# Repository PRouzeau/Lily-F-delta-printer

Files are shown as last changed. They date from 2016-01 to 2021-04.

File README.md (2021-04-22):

**"Lily" delta printer** built with strong wooden box structure and equipped with activated carbon filters<br>
The version 'F' is built with RRP Fisher components. Usable area diam 170mm x 242mm or diam 186mm x 225 mm<br>
To see the simulation of printer, run the "Delta_simulator.scad" in OpenScad <br>
The parameters of this simulation are defined in "data_Lily_F.scad" <br>
effector simulation use stl files created in "Effector_Lily_F.scad" <br>
To creates STL file, define a part Number in "data_Lily_F.scad" in OpenScad <br>
To creates STL files for the effector, define a part Number in "Effector_Lily_F.scad" in OpenScad <br>
<br>
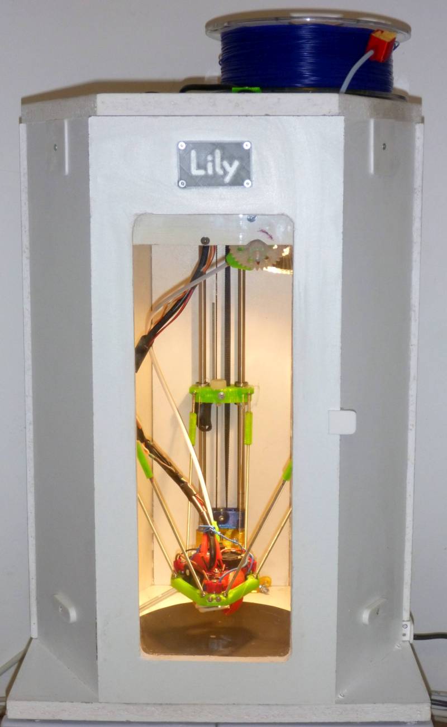
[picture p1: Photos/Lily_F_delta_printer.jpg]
Lily F photo, version D170xH242


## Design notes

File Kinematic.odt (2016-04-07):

As already published in this forum, I am using the wire tensioning system on my two printers since 6 month now, first on the D-Box http://rouzeau.net/Print3D/DBox, then on the Lily http://rouzeau.net/Print3D/Lily.

Retainers are magnets on the D-Box, and rubbers bands on the Lily, to save weight.

The bowden tube tend to pull the hotend support for probe points at the largest diameter, so I had to increase the hotend support pulling value to a minimum. I settled to ~1kg for both machines.

The repeatability is very good in a fixed context, however, the load needed to operate the ‘sensor’ make you machine to deflect of a significant amount, giving a probing offset. As the machine deformations are not the same on all the bed area, you shall individualise offset for each probe point, with calibration done with the sheet paper method.

The offset variability depends a lot of the overall machine stiffness. For the D-Box, I had initially an offset of ~0.4~-0.5mm, with a variability of ~0.15mm. When I replaced the arms by stiffer ones (the weak point was the screwing in plastic on the arms themselves), that reduced sufficiently the offset variability between all points that I abandoned individual offset to a common one, which is now a constant of 0.5 mm for all probing points.

The Lily, while a smaller machine, is a bit less robust (its mechanics cames from the Fisher Delta) and the offset variability remains significant throughout the bed, with values ranging from 0.35 to 0.45 (I have eliminated one point which is off plane).

The only problems I experienced so far :

*I had to retighten the standoffs as their screws tend to became loose with time.

*Heating the D-Box chamber (~70°C)/the bed (tested at 130°C) have driven to effector bending due to wire tension, needing to raise the effector to avoid magnet contacts making the sensor inoperative. The material used (PETG) cannot cope with these temperature tests.

In the Lily « F », there is only yet an halogen spot of 50W which raise slowly the chamber temperature to ~38°C while printing. I will install a heated bed of 100~120W, and will report the obtained temperature (expected below 55°C for Bed 100°C).

ABS may be a better material than PETG, but was not possible for me when I built both printers (no heat bed).

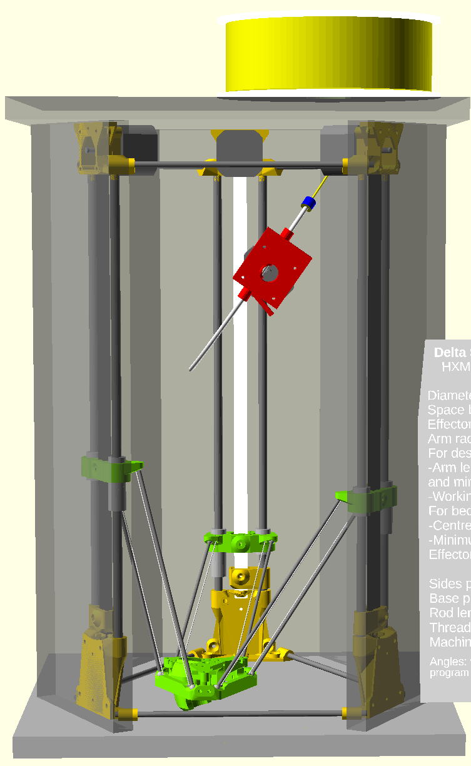
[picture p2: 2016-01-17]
Photos/Lily_F_simulation.png

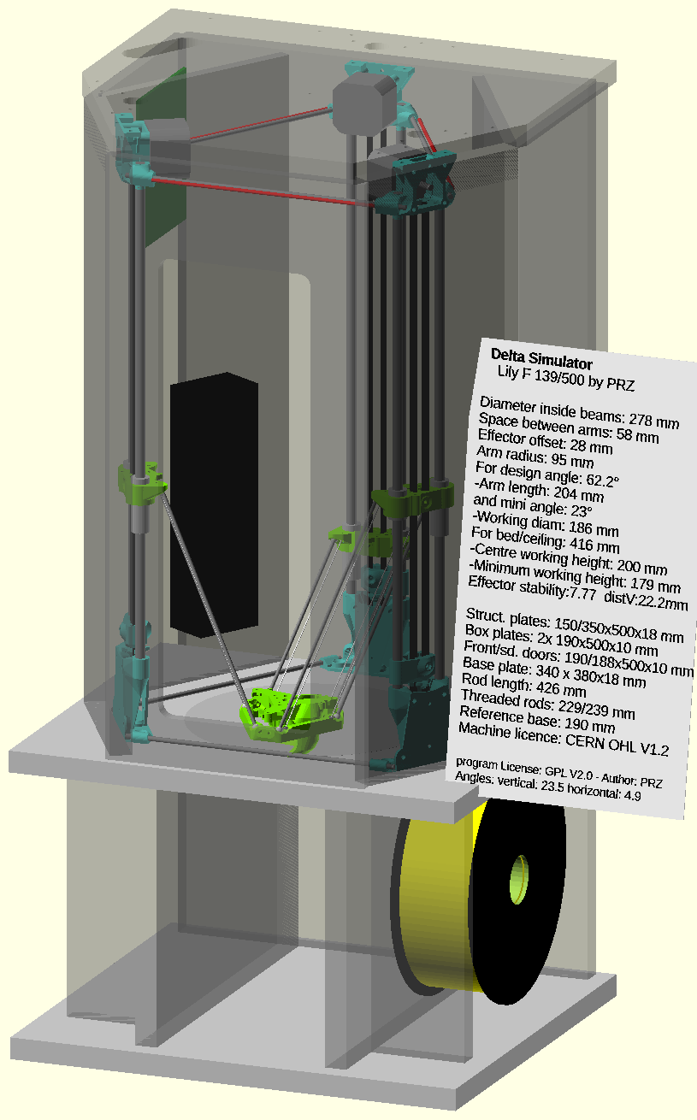
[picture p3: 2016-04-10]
Photos/Lily_F_with_support.png

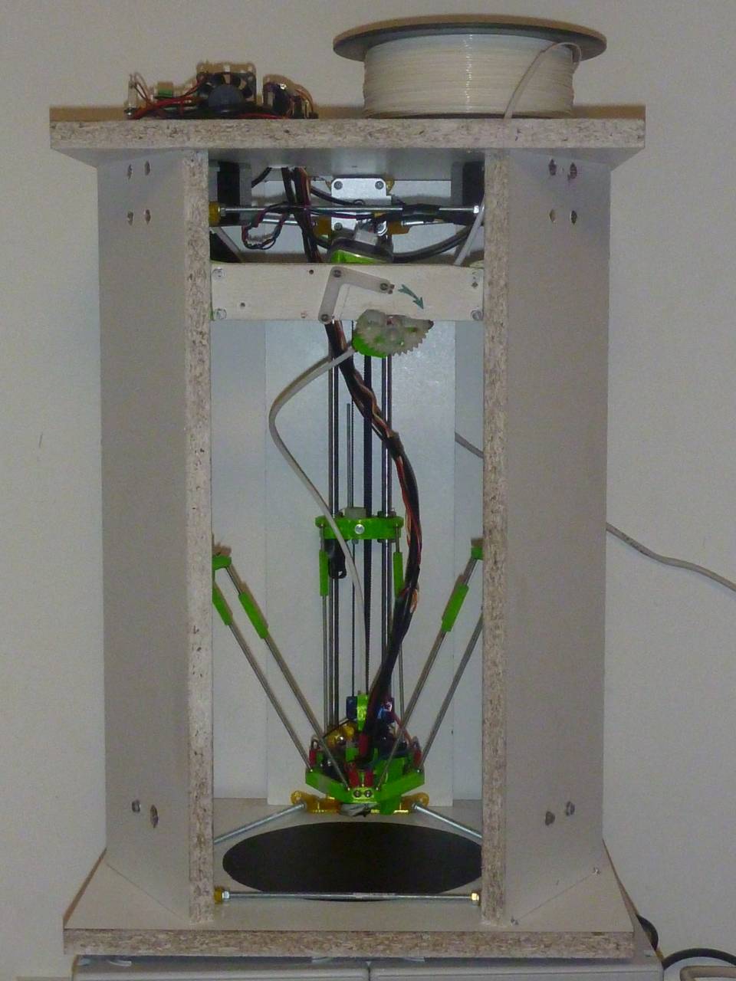
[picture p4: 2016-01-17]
Photos/Lily_F_not_enclosed.jpg

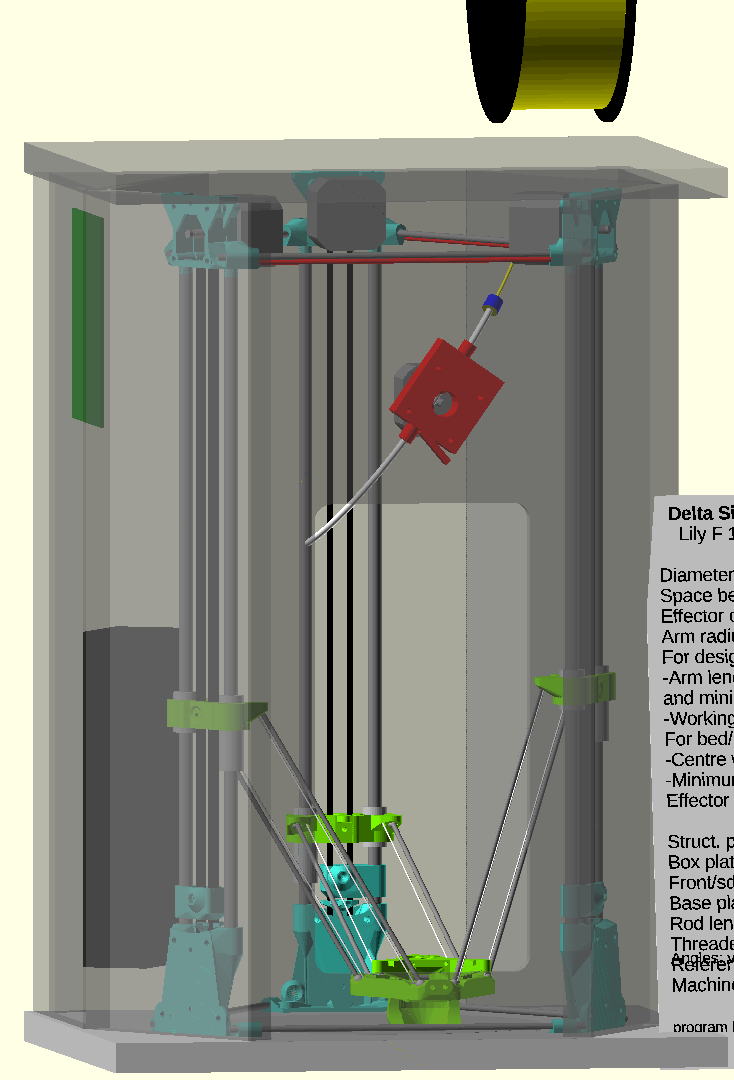
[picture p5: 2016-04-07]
Photos/Lily_F_simulation_boxed.png

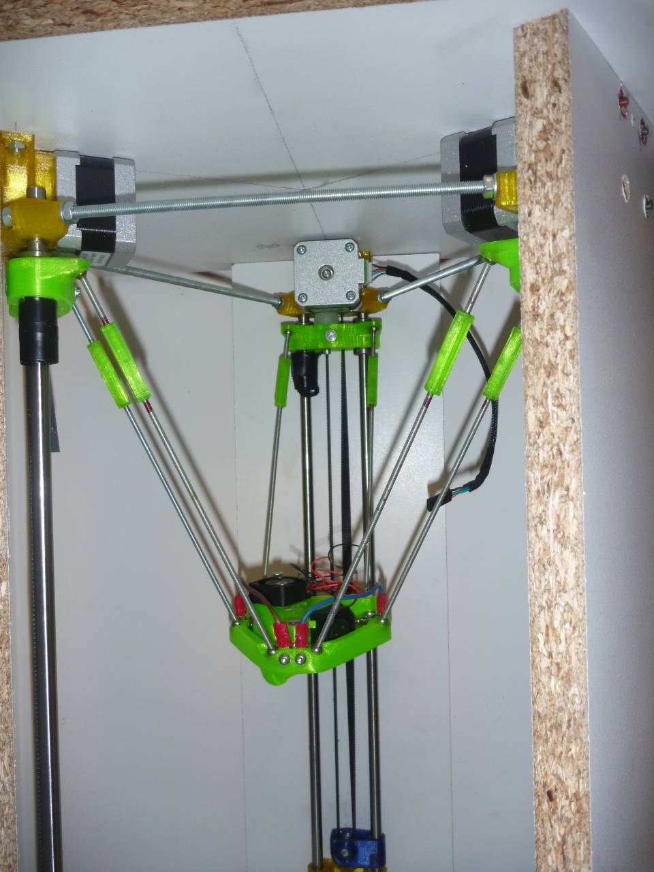
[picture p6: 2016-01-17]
Photos/Lily_F_motors.jpg

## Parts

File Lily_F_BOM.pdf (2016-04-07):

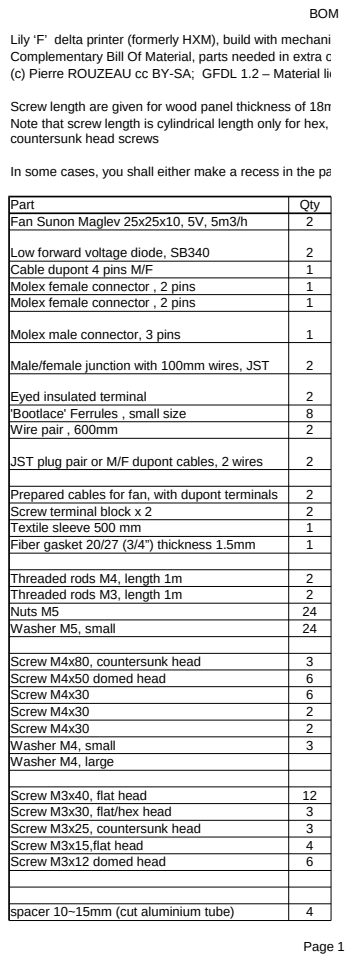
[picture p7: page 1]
BOM; Part; Qty; Fan Sunon Maglev 25x25x10, 5V, 5m3/h; Low forward voltage diode, SB340; Cable dupont 4 pins M/F; Molex female connector , 2 pins; Molex male connector, 3 pins; Male/female junction with 100mm wires, JST; Eyed insulated terminal; 'Bootlace' Ferrules , small size; Wire pair , 600mm; JST plug pair or M/F dupont cables, 2 wires; Prepared cables for fan, with dupont terminals; Screw terminal block x 2; Textile sleeve 500 mm; Fiber gasket 20/27 (3/4”) thickness 1.5mm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

Lily ‘F’ delta printer (formerly HXM), build with mechanical parts of the Fisher delta.
Complementary Bill Of Material, parts needed in extra of the Fisher parts
(c) Pierre ROUZEAU cc BY-SA; GFDL 1.2 – Material licence CERN OHL V1.2 – January 2016

Screw length are given for wood panel thickness of 18mm
Note that screw length is cylindrical length only for hex, flat, domed, .. head screws, but is total screw length for
countersunk head screws

In some cases, you shall either make a recess in the panel, or use cutted screws

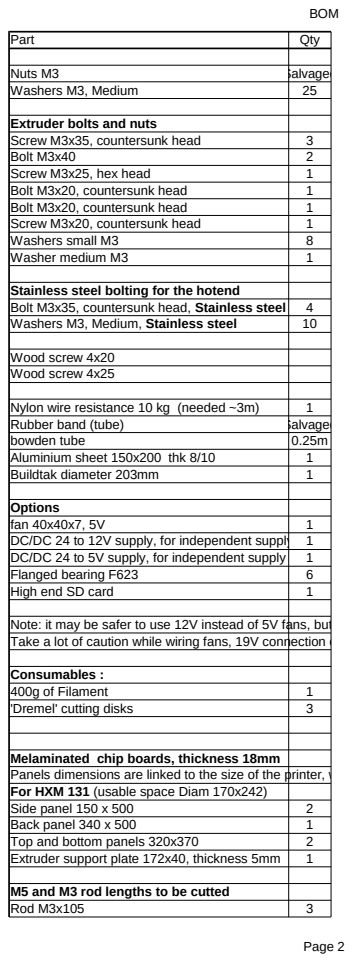
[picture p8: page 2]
Part; Qty; Nuts M3; Salvaged; Washers M3, Medium; Screw M3x35, countersunk head; Bolt M3x40; Screw M3x25, hex head; Bolt M3x20, countersunk head; Screw M3x20, countersunk head; Washers small M3; Washer medium M3; Wood screw 4x20 Wood screw 4x25; Nylon wire resistance 10 kg (needed ~3m); Rubber band (tube); bowden tube; Aluminium sheet 150x200 thk 8/10; Buildtak diameter 203mm; fan 40x40x7, 5V; DC/DC 24 to 5V supply, for independent supply; Flanged bearing F623; High end SD card; Consumables :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

Extruder bolts and nuts

Stainless steel bolting for the hotend
Bolt M3x35, countersunk head, Stainless steel
Washers M3, Medium, Stainless steel

Options
DC/DC 24 to 12V supply, for independent supply 1

Note: it may be safer to use 12V instead of 5V fans, but you need a DC/DC converter 19V→12V
Take a lot of caution while wiring fans, 19V connection on 5V input will burn the board

Melaminated chip boards, thickness 18mm
Panels dimensions are linked to the size of the printer, which is defined by the radius of the rod axis
For HXM 131 (usable space Diam 170x242)

M5 and M3 rod lengths to be cutted

Part | Qty
Measurement stick 172mm | 1
Rod M5x214 | 3
Rod M5x225 | 3
Rod M3x40 | 6
Rod M3x147 | 6

For HXM139/500
Measurement stick 188mm | 1
Rod M5x230 | 3
Rod M5x241 | 3
Rod M3x40 | 6
Rod M3x161 | 6

For HXM131/500 (usable space Diam 170x242)

Usage
hotend fan + part fan

Prolonge 1 motor wire
5V connection on board
Connect controlled fan on board – use only 1 wire

connect the fans on screw terminals Adjustable fan and effector sensor connection

Fan plugs on effector
Fan connection to 5V
Effector cables maintain
Hotend insulator

triangle, cuts 3x225, 3x214 arms 6x40, 6x147

triangle rods

Tensioner screw
bottom attach rod locks
bottom support attach to wall Top attach motor support
Top attach extruder
Tensioner screw

Motor attach
carriage lock
tensioner bearing shaft
extruder plate attach
kinematic cylinders

Board support

secure the fan power supply, other solution remove board LED

Connect fixed fan on existing loom – could be replaced by soldering
connect effector sensor and adjustable fan on hotend side
connect effector sensor standoff. Existing not usable because insufficient clearance

Connection of the calibration sensor and of the controlled fan on Effector

Usage

Salvaged

Motor attach
Tensioner
Main gear axis
Bearing axis
Lever axis
Motor attach

1rst washer on main gear

Hotend attach

arms tension
effector maintain
filament inlet
board cover
printing surface

board cooling
to use 12V fans instead of 5V – safer

belt pulleys
To speed up transfer – could go up to 350 kB/sec

The base material
To cut M3 rods. M5 rods are sawed

switch actuation (option)

Usage

Bottom triangle
Top triangle
Arm, short side
Arms, long side (for arms L190mm)

Bottom triangle
Top triangle
Arm, short side
Arms, long side (for arms L204mm)

Weights

Printed parts for Lily F delta Printer (c) Pierre ROUZEAU - cc BY-SA Weights in grams, time in minutes

Part | Weight | Comments
Tensioner | 7 | 60Layer 0.3
base support | 30 | 240Layer 0.3
motor support | 20 | 150Layer 0.3
carriage | 15 | 175Layer 0.3
rod joint | 2 | 20Layer 0.3
74 222
hotend support | 20 | 85Layer 0.25
effector | 19 | 48Layer 0.3
39
arm links (6) | - | 8 | Layer 0.3
extruder base | 16 | 50Layer 0.25
extruder lever | 7 | - | Layer 0.2
pinion | 4 | - | Layer 0.2
gear | 8 | 90Layer 0.2 | gears+lever common print
35
Extruder plate brackets | 7 | 7 | 20Layer 0.3
Spool support | - | - | Layer 0.3
Axis | - | Layer 0.3
Spool ring | - | 30- | Layer 0.3
90 | all spool

341
15.30

Direct extruder print is only 50 min, so that same 1h and an half on printing time.

The hotend support shall absolutely be in plastic somewhat resistant to heat. PLA WILL melt.

The given times are for a hotend with long heat zone adapted for PETG printing.
Also, there is controlled cooling, which allow shorter cooling time and faster prints for some parts For the fisher, printing time may be increased approximately by 20%

Time
(total)

If printed on the Fisher in PETG, there is no point to print in layer 0.3, as the extruder cannot have sufficient flowrate at 80 mm/s, so you could print with layer 0.3 and reduced speed (~50mm/s) or with layers 0.25 at full speed (80 mm/s). Temperature shall be high, but you may face problems for parts with bridging or small area.

Weights Standard

Printed parts for Lily ‘F’ (formerly HXM) delta Printer (c) Pierre ROUZEAU - cc BY-SA Weights in grams, time in minutes

Part | Nb | Weight | Comments
Tensioner | 6 or 7 | 7 | | 60Layer 0.3
foot | 2 | 12 | - | Layer 0.3
Intermediate support | 3 | 7 | | 145Layer 0.3
motor support | 4 | 20 | | 150Layer 0.3
carriage | 5 | 15 | | 175Layer 0.3
tensioner thumbwheel | 8 | 1 | | 5Layer 0.3
arm links (6) | 9 | 2 | | 20Layer 0.3
| | 64 192
hotend support 1 | | 9 | - | Layer 0.3
hotend support 2 | | 6 | | 38Layer 0.3
effector | | 19 | | 48Layer 0.3
Duct | 4 | 15
28
Direct extruder base | | 10 | - | Layer 0.3
Tensioner | | 1 | - | Layer 0.3
extruder lever | | 6 | - | Layer 0.25
thumbwheel | | 1 | | Layer 0.25
55
18
Extruder plate brackets | 7 | 7 | 20Layer 0.3
Board supports | 11 | 4 | | 14Layer 0.3
Glass supports | 8 | 24
12
Spool support | | - | - | Layer 0.3
Axis | | - | | Layer 0.3
Spool ring | | - | 30 - | Layer 0.3
90 | all spool

287
| | | 14.32

The hotend support shall absolutely be in plastic somewhat resistant to heat. PLA WILL melt.

The given times are for a hotend with long heat zone adapted for PETG printing.
Also, there is controlled cooling, which allow shorter cooling time and faster prints for some parts

Time
(total)
Part 6 for plain bearings, part 7 for flanged bearings

If printed on the Fisher in PETG, there is no point to print in layer 0.3, as the extruder cannot have sufficient flowrate at 80 mm/s, so you could print with layer 0.3 and reduced speed (~50mm/s) or with layers 0.25 at full speed (80 mm/s). Temperature shall be high, but you may face problems for parts with bridging or small area.

Weights Standard

For the fisher, printing time may be increased approximately by 20%

Weights Standard

“c:\Program Files\OpenSCAD\
“c:\Program Files\OpenSCAD\openscad” data_HXM.scad

'c:\Program Files\OpenSCAD\openscad.exe' -o Lily_part3 -D part=3 data_HXM.scad

Weights Standard

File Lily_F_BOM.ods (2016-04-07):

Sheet: BOM
Lily ‘F’ delta printer (formerly HXM), build with mechanical parts of the Fisher delta.
Complementary Bill Of Material, parts needed in extra of the Fisher parts
(c) Pierre ROUZEAU cc BY-SA; GFDL 1.2 – Material licence CERN OHL V1.2 – January 2016
Screw length are given for wood panel thickness of 18mm
Note that screw length is cylindrical length only for hex, flat, domed, .. head screws, but is total screw length for countersunk head screws
In some cases, you shall either make a recess in the panel, or use cutted screws
Part | Qty | Usage
Fan Sunon Maglev 25x25x10, 5V, 5m3/h | 2 | hotend fan + part fan
Low forward voltage diode, SB340 | 2 | secure the fan power supply, other solution remove board LED
Cable dupont 4 pins M/F | 1 | Prolonge 1 motor wire
Molex female connector , 2 pins | 1 | 5V connection on board
Molex female connector , 2 pins | 1 | Connect controlled fan on board – use only 1 wire
Molex male connector, 3 pins | 1 | Connect fixed fan on existing loom – could be replaced by soldering
Male/female junction with 100mm wires, JST | 2 | connect effector sensor and adjustable fan on hotend side
Eyed insulated terminal | 2 | connect effector sensor standoff. Existing not usable because insufficient clearance
'Bootlace' Ferrules , small size | 8 | connect the fans on screw terminals
Wire pair , 600mm | 2 | Adjustable fan and effector sensor connection
JST plug pair or M/F dupont cables, 2 wires | 2 | Connection of the calibration sensor and of the controlled fan on Effector
Prepared cables for fan, with dupont terminals | 2 | Fan plugs on effector
Screw terminal block x 2 | 2 | Fan connection to 5V
Textile sleeve 500 mm | 1 | Effector cables maintain
Fiber gasket 20/27 (3/4”) thickness 1.5mm | 1 | Hotend insulator
Threaded rods M4, length 1m | 2 | triangle, cuts 3x225, 3x214
Threaded rods M3, length 1m | 2 | arms 6x40, 6x147
Nuts M5 | 24
Washer M5, small | 24 | triangle rods
Screw M4x80, countersunk head | 3 | Tensioner screw
Screw M4x50 domed head | 6 | bottom attach rod locks
Screw M4x30 | 6 | bottom support attach to wall
Screw M4x30 | 2 | Top attach motor support
Screw M4x30 | 2 | Top attach extruder
Washer M4, small | 3 | Tensioner screw
Washer M4, large
Screw M3x40, flat head | 12 | Motor attach
Screw M3x30, flat/hex head | 3 | carriage lock
Screw M3x25, countersunk head | 3 | tensioner bearing shaft
Screw M3x15,flat head | 4 | extruder plate attach
Screw M3x12 domed head | 6 | kinematic cylinders
spacer 10~15mm (cut aluminium tube) | 4 | Board support
Nuts M3 | Salvaged
Washers M3, Medium | 25
Extruder bolts and nuts
Screw M3x35, countersunk head | 3 | Motor attach
Bolt M3x40 | 2 | Tensioner
Screw M3x25, hex head | 1 | Main gear axis
Bolt M3x20, countersunk head | 1 | Bearing axis
Bolt M3x20, countersunk head | 1 | Lever axis
Screw M3x20, countersunk head | 1 | Motor attach
Washers small M3 | 8
Washer medium M3 | 1 | 1rst washer on main gear
Stainless steel bolting for the hotend
Bolt M3x35, countersunk head, Stainless steel | 4 | Hotend attach
Washers M3, Medium, Stainless steel | 10
Wood screw 4x20
Wood screw 4x25
Nylon wire resistance 10 kg (needed ~3m) | 1 | arms tension
Rubber band (tube) | Salvaged | effector maintain
bowden tube | 0.25m | filament inlet
Aluminium sheet 150x200 thk 8/10 | 1 | board cover
Buildtak diameter 203mm | 1 | printing surface
Options
fan 40x40x7, 5V | 1 | board cooling
DC/DC 24 to 12V supply, for independent supply | 1 | to use 12V fans instead of 5V – safer
DC/DC 24 to 5V supply, for independent supply | 1
Flanged bearing F623 | 6 | belt pulleys
High end SD card | 1 | To speed up transfer – could go up to 350 kB/sec
Note: it may be safer to use 12V instead of 5V fans, but you need a DC/DC converter 19V→12V
Take a lot of caution while wiring fans, 19V connection on 5V input will burn the board
Consumables :
400g of Filament | 1 | The base material
'Dremel' cutting disks | 3 | To cut M3 rods. M5 rods are sawed
Melaminated chip boards, thickness 18mm
Panels dimensions are linked to the size of the printer, which is defined by the radius of the rod axis
For HXM 131 (usable space Diam 170x242)
Side panel 150 x 500 | 2
Back panel 340 x 500 | 1
Top and bottom panels 320x370 | 2
Extruder support plate 172x40, thickness 5mm | 1
M5 and M3 rod lengths to be cutted
Rod M3x105 | 3 | switch actuation (option)
For HXM131/500 (usable space Diam 170x242)
Measurement stick 172mm | 1
Rod M5x214 | 3 | Bottom triangle
Rod M5x225 | 3 | Top triangle
Rod M3x40 | 6 | Arm, short side
Rod M3x147 | 6 | Arms, long side (for arms L190mm)
For HXM139/500
Measurement stick 188mm | 1
Rod M5x230 | 3 | Bottom triangle
Rod M5x241 | 3 | Top triangle
Rod M3x40 | 6 | Arm, short side
Rod M3x161 | 6 | Arms, long side (for arms L204mm)

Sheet: Weights
Printed parts for Lily F delta Printer (c) Pierre ROUZEAU - cc BY-SA
Weights in grams, time in minutes
Part | Weight |  | Time (total) |  | Comments
Tensioner | 7 |  | 60 | Layer 0.3
base support | 30 |  | 240 | Layer 0.3
motor support | 20 |  | 150 | Layer 0.3
carriage | 15 |  | 175 | Layer 0.3
rod joint | 2 |  | 20 | Layer 0.3
 | 74 | 222
hotend support | 20 |  | 85 | Layer 0.25
effector | 19 |  | 48 | Layer 0.3
 |  | 39
arm links (6) | - | 8 |  | Layer 0.3
extruder base | 16 |  | 50 | Layer 0.25
extruder lever | 7 |  | - | Layer 0.2
pinion | 4 |  | - | Layer 0.2
gear | 8 |  | 90 | Layer 0.2 | gears+lever common print
 |  | 35
Extruder plate brackets | 7 | 7 | 20 | Layer 0.3
Spool support | - |  | - | Layer 0.3
Axis | - |  |  | Layer 0.3
Spool ring | - | 30 | - | Layer 0.3
 |  |  | 90 |  | all spool
 |  | 341
 |  |  | 15.30
Direct extruder print is only 50 min, so that same 1h and an half on printing time.
If printed on the Fisher in PETG, there is no point to print in layer 0.3, as the extruder cannot have sufficient flowrate at 80 mm/s, so you could print with layer 0.3 and reduced speed (~50mm/s) or with layers 0.25 at full speed (80 mm/s). Temperature shall be high, but you may face problems for parts with bridging or small area.
The hotend support shall absolutely be in plastic somewhat resistant to heat. PLA WILL melt.
The given times are for a hotend with long heat zone adapted for PETG printing.
Also, there is controlled cooling, which allow shorter cooling time and faster prints for some parts
For the fisher, printing time may be increased approximately by 20%

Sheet: Weights Standard
Printed parts for Lily ‘F’ (formerly HXM) delta Printer (c) Pierre ROUZEAU - cc BY-SA
Weights in grams, time in minutes
Part | Nb | Weight |  | Time (total) |  | Comments
Tensioner | 6 or 7 | 7 |  | 60 | Layer 0.3 | Part 6 for plain bearings, part 7 for flanged bearings | “c:\Program Files\OpenSCAD\openscad” -o Lily_part11.stl -Dpart=11 data_HXM.scad | 'c:\Program Files\OpenSCAD\openscad.exe' -o Lily_part3 -D part=3 data_HXM.scad
foot | 2 | 12 |  | - | Layer 0.3 |  | “c:\Program Files\OpenSCAD\openscad” data_HXM.scad
Intermediate support | 3 | 7 |  | 145 | Layer 0.3
motor support | 4 | 20 |  | 150 | Layer 0.3
carriage | 5 | 15 |  | 175 | Layer 0.3
tensioner thumbwheel | 8 | 1 |  | 5 | Layer 0.3
arm links (6) | 9 | 2 |  | 20 | Layer 0.3
 |  | 64 | 192
hotend support 1 |  | 9 |  | - | Layer 0.3
hotend support 2 |  | 6 |  | 38 | Layer 0.3
effector |  | 19 |  | 48 | Layer 0.3
Duct |  | 4 |  | 15
 |  |  | 28
Direct extruder base |  | 10 |  | - | Layer 0.3
Tensioner |  | 1 |  | - | Layer 0.3
extruder lever |  | 6 |  | - | Layer 0.25
thumbwheel |  | 1 |  |  | Layer 0.25
 |  |  |  | 55
 |  |  | 18
Extruder plate brackets |  | 7 | 7 | 20 | Layer 0.3
Board supports | 11 | 4 |  | 14 | Layer 0.3
Glass supports |  | 8 |  | 24
 |  |  | 12
Spool support |  | - |  | - | Layer 0.3
Axis |  | - |  |  | Layer 0.3
Spool ring |  | - | 30 | - | Layer 0.3
 |  |  |  | 90 |  | all spool
 |  |  | 287
 |  |  |  | 14.32
If printed on the Fisher in PETG, there is no point to print in layer 0.3, as the extruder cannot have sufficient flowrate at 80 mm/s, so you could print with layer 0.3 and reduced speed (~50mm/s) or with layers 0.25 at full speed (80 mm/s). Temperature shall be high, but you may face problems for parts with bridging or small area.
The hotend support shall absolutely be in plastic somewhat resistant to heat. PLA WILL melt.
The given times are for a hotend with long heat zone adapted for PETG printing.
Also, there is controlled cooling, which allow shorter cooling time and faster prints for some parts
For the fisher, printing time may be increased approximately by 20%

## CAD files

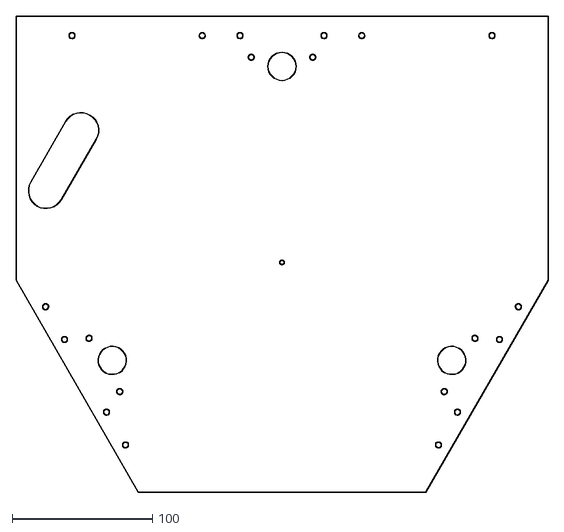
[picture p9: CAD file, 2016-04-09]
DXF/Lily_F_139_500_65_top_panel.dxf
380.0 x 340.0

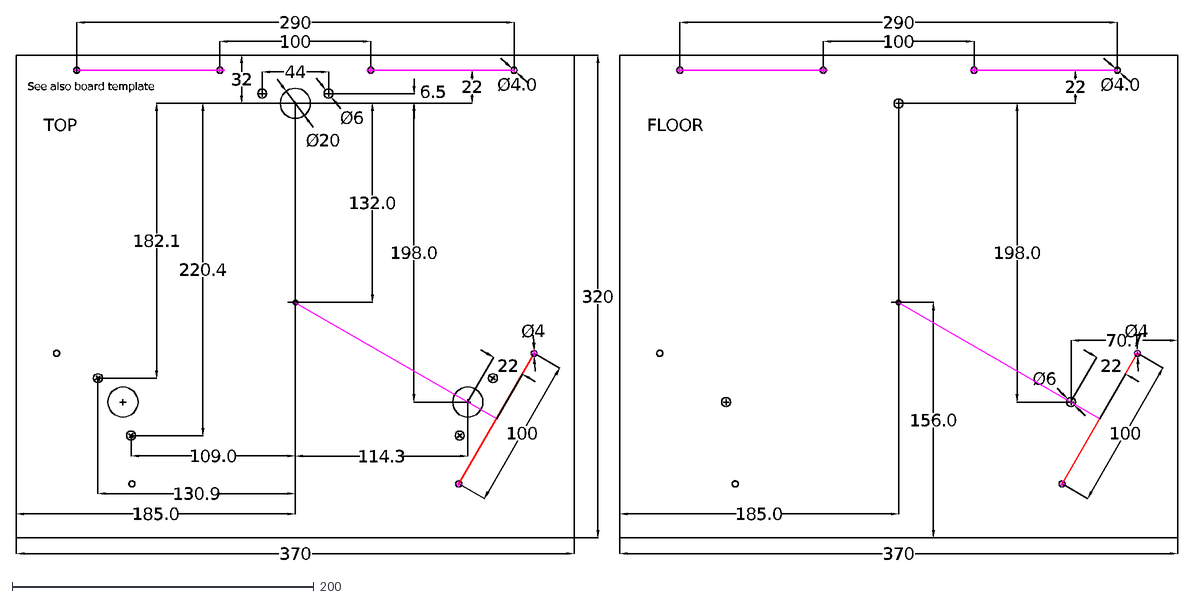
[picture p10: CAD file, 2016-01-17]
Lily_F_131_500_top_bottom_template.dxf
198.0
114.3
32
185.0
6.5
44
130.9
109.0
220.4
182.1
132.0
TOP
Ø20
Ø6
70.7
320
156.0
FLOOR
See also board template
Ø4.0
100
22
290
Ø4
370

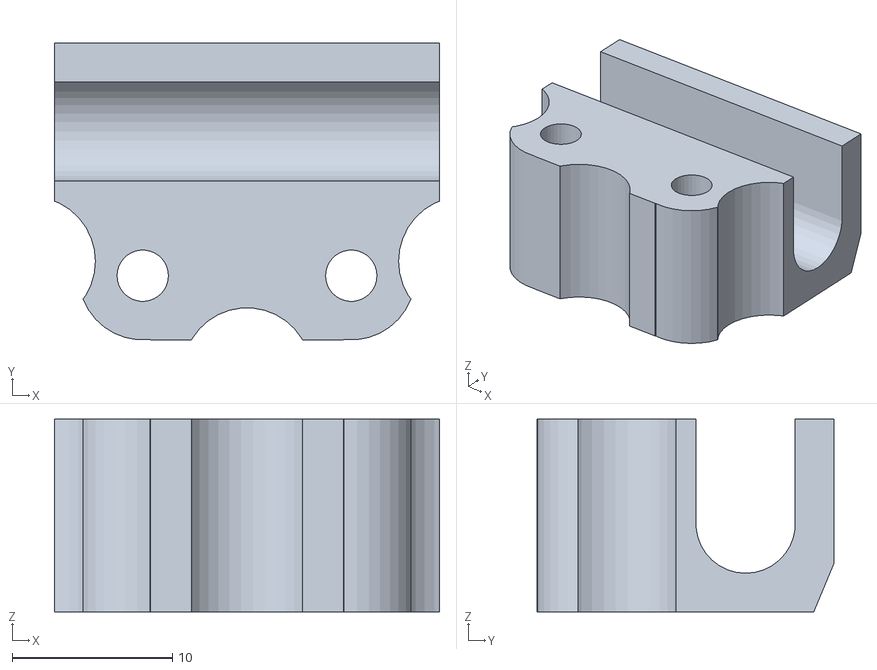
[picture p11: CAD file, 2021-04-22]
STL/Lily_32_cable_retainer.stl
24.0 x 18.5 x 12.0

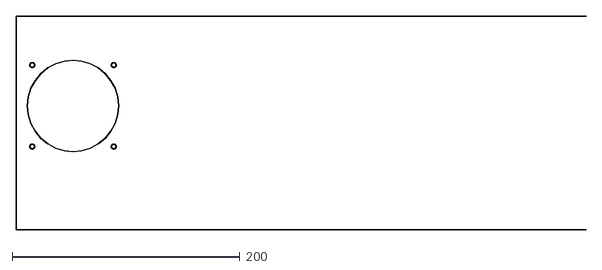
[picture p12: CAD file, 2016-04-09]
DXF/Lily_F_139_500_55_left_door.dxf
500.0 x 187.5

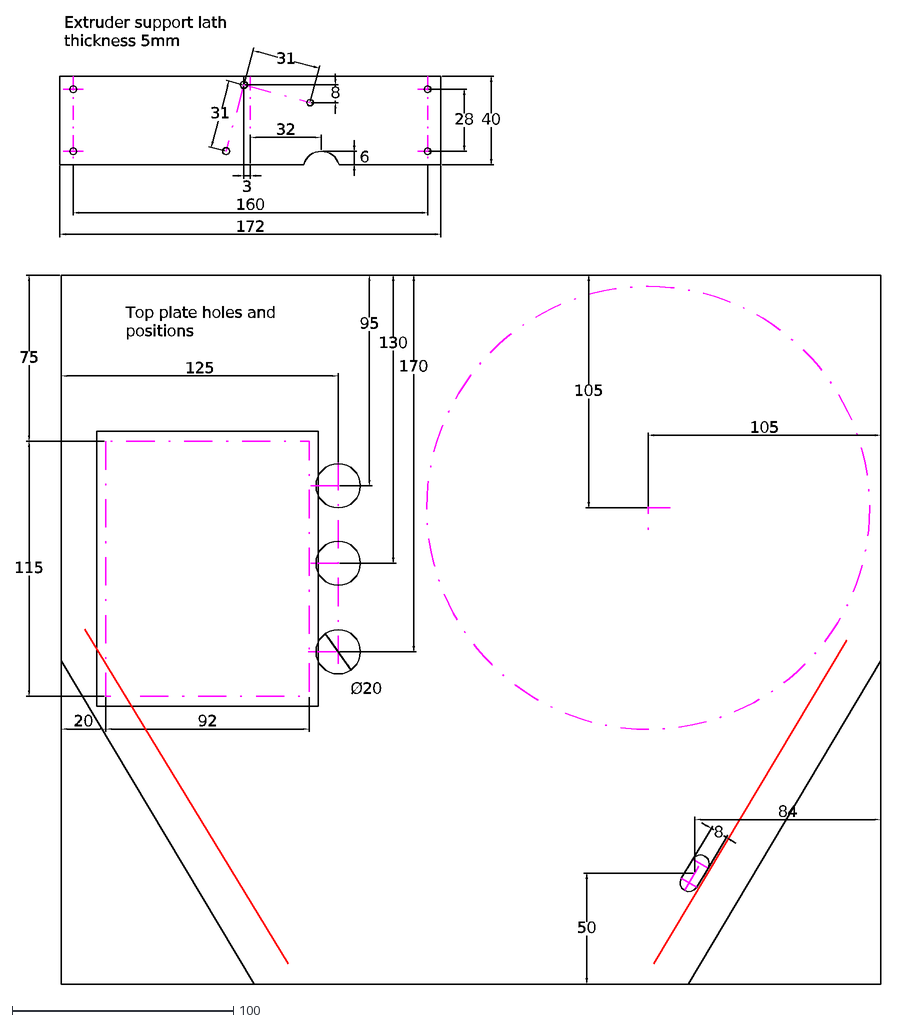
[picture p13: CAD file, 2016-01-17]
Lily_F_131_500_board_pos.dxf
20
92
75
115
125
130
170
105
84
50
95
8
31
3
172
160
40
28
32
6
Extruder support lath thickness 5mm
Ø20
Top plate holes and positions

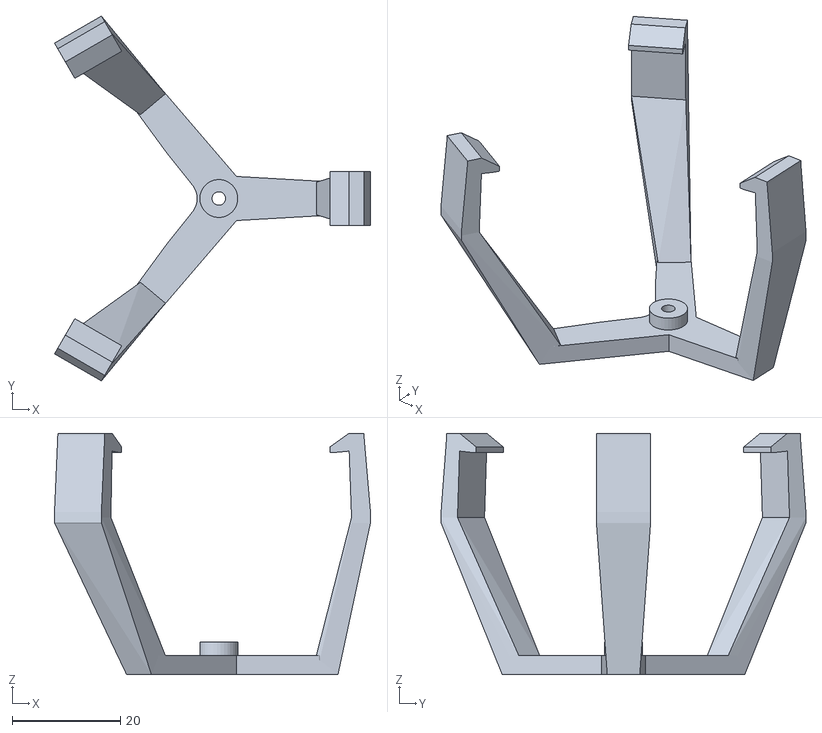
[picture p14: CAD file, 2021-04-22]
STL/Lily_33_effector_retainer.stl
58.3 x 67.4 x 44.5

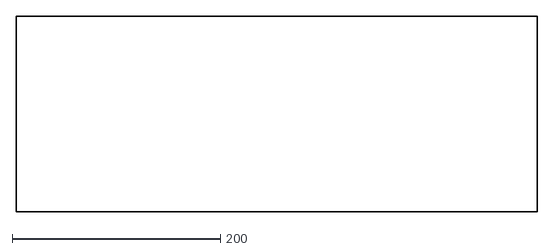
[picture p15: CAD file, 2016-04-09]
DXF/Lily_F_139_500_56_right_door.dxf
500.0 x 187.5

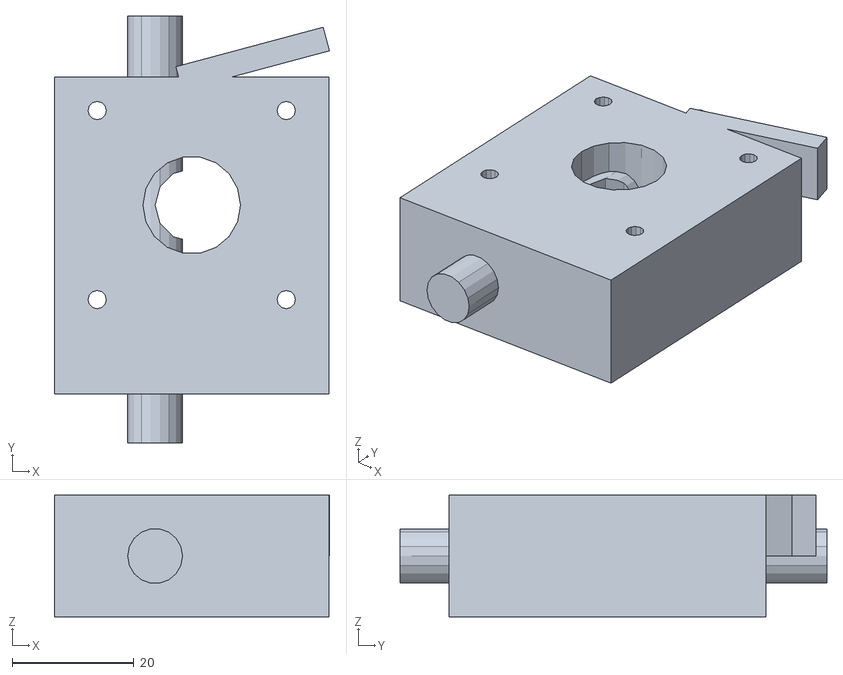
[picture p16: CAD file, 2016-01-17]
extruder.stl
45.1 x 70.0 x 20.0

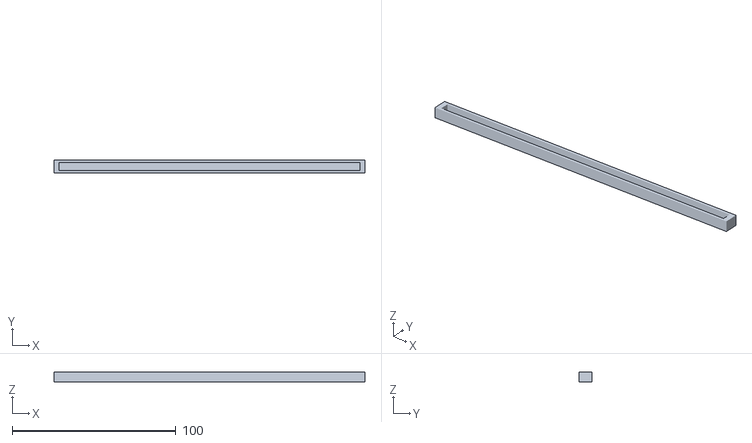
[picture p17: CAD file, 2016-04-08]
STL/Lily_F_139_reference_stick.stl
189.9 x 8.00 x 6.00

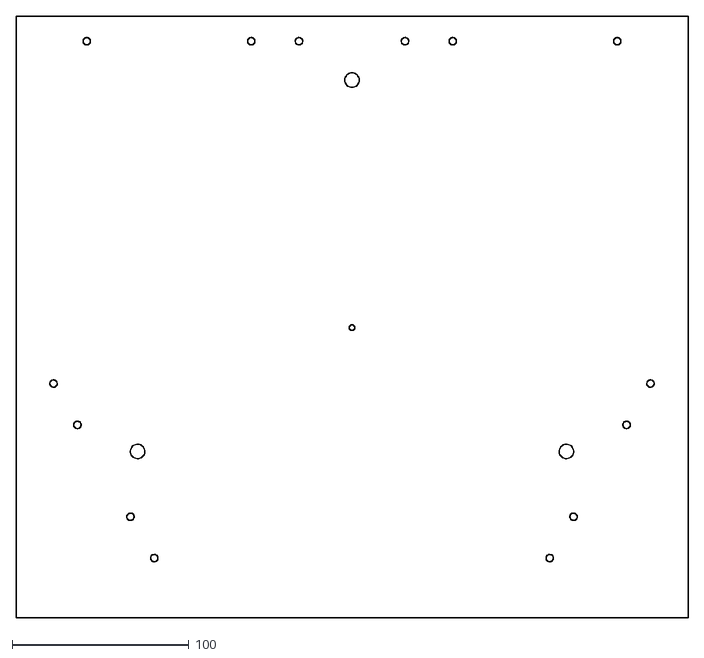
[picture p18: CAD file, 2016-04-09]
DXF/Lily_F_139_500_61_bottom.dxf
380.0 x 340.0

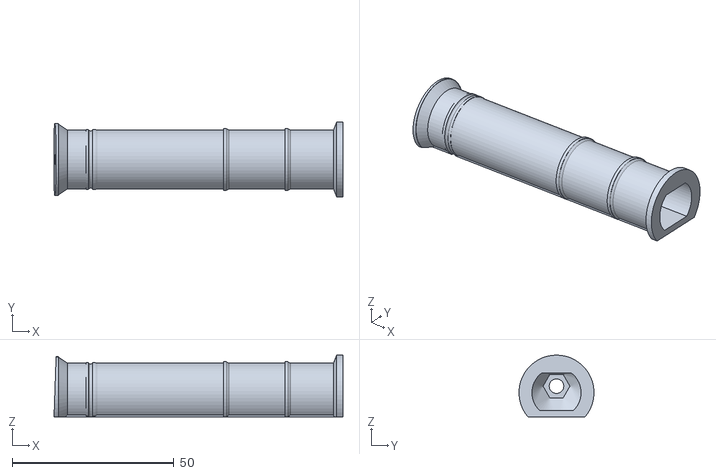
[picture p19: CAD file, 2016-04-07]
STL/Spigot90.stl
89.3 x 23.2 x 19.1

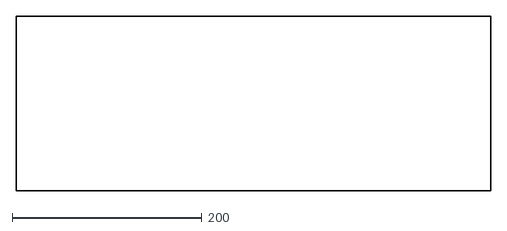
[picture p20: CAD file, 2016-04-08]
DXF/Lily_F_139_500_53_left_side.dxf
500.0 x 184.2

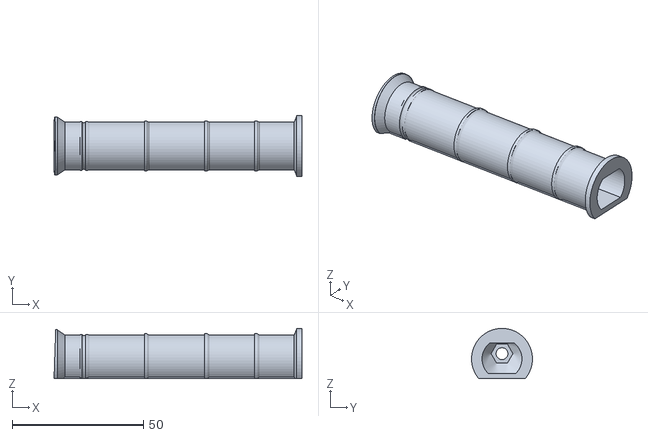
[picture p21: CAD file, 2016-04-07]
STL/Spigot95.stl
94.3 x 23.2 x 19.1

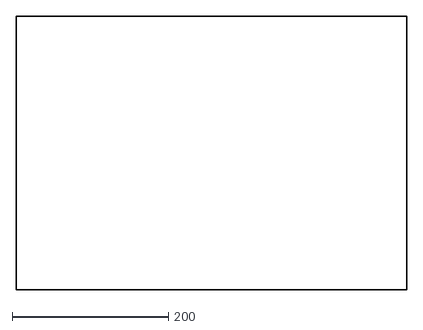
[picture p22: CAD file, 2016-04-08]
DXF/Lily_F_139_500_52_back_panel.dxf
500.0 x 350.0

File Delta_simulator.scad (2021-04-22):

// Parallel columns delta robot simulator, extracted from my Delta printer design.
// This simulator could emulate any delta travels, provided the parameters are accurate.
// Needs OpenScad 2015.03 or, for animations, the nightly versions.

// Play with it! you won't broke anything. See line 92 for existing datasets. 

// To run the animation click [View][Animate],a panel open in the bottom right of your screen. Set 10~25 in the FPS fied and 360 in the field 'Steps'. A lower number will make larger steps. You can manipulate the view during animation. 
// OpenScad official version 2015.03 have a lot of flickering during animation. This is corrected in the nightly versions, which I recommended to use.  
// Licence GPL V2.0 - Pierre ROUZEAU aka PRZ - 
// version 0.4.3 - 12 June 2015
// 25 May 2015 - add twin rods in addition of extrusion - display bot name - modifs for micros deltas (Fisher delta and Micro Delta) - allow user part build for effector, corners and carriage.
// 29 may 2015 - added internal comments to explain use. Frame order build modified for tranparent panels
// June - allow more personnalisation - review fan , spool - allow dataset text lines
// 12 June 15: 'square Delta' - 29 sept 15 'Zatsit' folded mechanic

//??? modifs -> Inversion rotation/translation on spool
//-- Data not redefined in dataset -------
$bArm= false;
$xtxt = 0; //???
$bdist = 0; // ? undef ?
$isAngle = false; // This is for Lily Big with steel angle rails
$extrusionwd = 0;

/*[Display]*/
//Build all the frame
$bAllFrame=true;
//Show details
$details=false;
//Remove box top
$noTop = false;
//Remove top column supports
$noTopSup = false;
//Complete Box (else only structural panels)
$boxed = true;
//Show side panels *in addition* to frame
$bSide = true; 
//??
$noCover=false;



/*[Movement]*/ 
//If no animation, the position is imposed by coordinates
panimation=false;
//hotend x coordinate - stay inside 
xe=50; 
//hotend y coordinate
ye=50;
//hotend z coordinate 
ze=0; 

/*/dimensions are in mm.
Delta_name = "Simulator example";
//-- Frame data -------------------------
beam_int_radius = 175; // radius inside the rectangular columns - used as reference radius
 // if columns are replaced with rods this is the radius of the rod axis plane. 
hbase = 60; // height of the base structure
htotal = 680; // total height, including base and top structure
bed_level = 8; // distance between the top of the bottom structure and the top of the bed.
extrusion = 20;
rod_space = 0; //if > 0 set two rods instead of one extrusion, diameter based on extrusion
  // if set, reference radius is rod axis plane and not extrusion face  
railthk   = 0;  // rail thickness. if > 0, show a cuboid simulating a sliding rail
railwidth = 0; 
rail_base = 0; // base of the rail, which could be higher than bed plate

//-- Carriage data --------------------
car_hor_offset=20; //Carriage: horizontal distance between the articulation and the internal of the columns
car_vert_dist=27;  //Carriage: vertical articulation distance/reference plane (at the top of the carriage) 
hcar=75; // carriage height - no effect on travel
dia_ball = 10; 
dia_arm  = 68;

//-- Effector data ----------------------
eff_hor_offset=28; //Distance effector center/articulations Kossel mini: 20, Rostock max: 33mm
eff_vert_dist = 12; //Vertical distance between the bottom of effector and the articulations axis

//-- General design data ----------------
arm_space=50; // space between the arms
wire_space = 0 ; // space between tensioning wire
top_clearance=10; // clearance between top of the carriage and top structure
delta_angle = 62; //key travel design: arm angle/horizontal for centered effector.
//Will only define the arm length and travels. Does not modify parts. 57~63°
//62° gives slightly longer arms and a near maximum practical usable space with vertical arms while nearing columns (if the iminimum angle is 20°). For a 3D printer, great care shall be done while installing fans which could easily conflict with columns. fan shall be installed 60° from the column and protrude on flat side.
//Reachable area is a rounded triangular shape, with the ends pointed on columns, hence the real limitation of travel is dictated by the clearance on columns. You have the option to define a rough belt simulation, which will show the conflicts - see below.
//  A clever positioning allows elongated parts to be slightly longer than the theoretical usable diameter

arm_length = 0; // Alternatively, you could define the arm length, which will supersedes the design angle - If too long, you will have problem with the animation (reachable area too large drive to overpass vertical for the arms). Set to 0 give priority to the angle. arm length is given axis to axis. 
 
mini_angle = 20; //minimum angle/horizontal. 20° is generally considered as the practical limit. That will not modify the design, only give you an approximate information  about the maximum possible range. The range is not really circular, but will be considered so for practical reasons. You could go below 20°, but there is no real point, because when the other arms are nearing vertical, the effector bang the columns. Also, it drives to dynamic problems (a small effector move need a large carriage move), extra loads and effector loss of stability.

hotend_vert_dist = 20;//vertical distance between hotend nozzle and effector bottom plate. depends from the effector design and hotend type.

//Frame details
frame_corner_radius=1.5*extrusion; //modify corner shape radius.
frame_face_radius=280; // radius of the face. Shall be >> overall radius. 0 is flat
corner_offset = -3; //offset center of the corner sector / beam internal radius
housing_base = 0; // if = 0 no housing shown - usually set to hbase
housing_opening = 300;
belt_dist=0; //distance between the belt and the internal of the column. (belt face at the contact point with effector). if this data is different from 0, rough belt approximation will be shown, for conflict evaluation.


spool_diam = 200; // if spool_diameter > 0, spool shown on top - vertical axis
spool_thk  = 70;

//-- Miscellaneous stuff - no influence on movement ---
struct_color = "red";
moving_color = "deepskyblue";
bed_color = [0.5,0.5,0.5,0.5]; // transparent 

//Geometry
move_rot  = 0;
frame_rot = 30;

//--- Text display -----------------------
txtangle= -60;
txtzpos = 320;

//*/

/*[Hidden]*/
// geometry
rotAng2 = 120; // added angles definition for 'square' delta - see specific dataset
rotAng3 = 240;
railrot = -30;

//Indicate that the program just started (to impose camera position)
camPos = $vpr==[55,0,25];

/*
$vpd=camPos?2100:$vpd;      // camera distance: work only if set outside a module
$vpr=camPos?[80,0,42]:$vpr; // camera rotation
$vpt=camPos?[215,-90,420]:$vpt; //camera translation  */

//== data set included below will supersedes above data 
include <data_Lily_F.scad>  //- Data set for Hexagon minimum by PRZ
//=======================================
//$details=true;
//qpart = 1;

//--- Text display -----------------------
txtsize = beam_int_radius/16;
txtxpos = 0.8*beam_int_radius;
txtypos = 1.22*beam_int_radius;

//------------------------------------------
$fn=32; // smooth the cylinders

//$t=0.8377;

//-- imposing effector position (if defined, this will supersedes the animation equation)
// note that structure is rotated 30°, so x and y are rotated accordingly.

//Alternatively, you could impose the position in polar coordinates
/*
e_radius=90;
e_angle=-89;
ze=213; 
xe=e_radius*cos(e_angle);
ye=e_radius*sin(e_angle);   //*/

// if you ask for an unreachable point, arms and effector will not be displayed, without warning.

// Displayed angles are those of the arms attached to the back column
// Note that for long arms, the side angles you can see may not be acceptable for rod ends type 'traxxas', 'Igus' or equivalent and are a very limiting factor for the reachable area.

//echo_camera();

//=======================================
view(); //The animation will run around a cylinder based on the maximum reachable radius at the middle of the columns. If arms are sufficiently long, it will bang on columns, belts, etc.
*view_circle (working_dia,0); // view_circle (dia, height) - if off-limits - display may fail
// view_helix (); 

//--- dimensions calculations -----------
radius_cent = beam_int_radius-eff_hor_offset-car_hor_offset;
ar_length = (arm_length)?arm_length: radius_cent/cos(delta_angle); // center to center
d_angle = acos(radius_cent/ar_length);
ht_cent = radius_cent*tan(d_angle);
working_dia =2*(ar_length*cos(mini_angle)-beam_int_radius+car_hor_offset+eff_hor_offset);  
// calculate the maximum usable height - at center - at sides
// reference plane is the base of the effector
effVtPos = hbase+bed_level+hotend_vert_dist; // height of effector base plane; 
// add the base height
carVtPos =effVtPos +(ht_cent+car_vert_dist+eff_vert_dist); //top of carriage vertical position while the head is at bed level
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

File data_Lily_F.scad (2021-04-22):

include <Z_library.scad>  
include <X_utils.scad>
// Data Set for Delta printer -LilY - Jan-april 2015
// To be build from scratch (Lily 'S'), or with  standard Fisher components (Lily 'F')
// Copyright Pierre ROUZEAU AKA 'PRZ'
// Program license GPL 2.0
// documentation licence cc BY-SA and GFDL 1.2
// Design licence CERN OHL V1.2

part=0; //[0:None -Library-, 1:Elevated foot (Fisher rods), 2:Flat foot (rods down to floor), 3:Wall support (for non elevated foot), 4:Motor_support, 5:Carriage, 6:Tensioner for plain bearing, 7:Tensioner for flanged bearing,8:Tensioner wheels, 9:Arm junctions, 10:Extruder bracket, 11:Board support, 12:Glass lock, 14:Power brick retainer, 15:Lily Name plate, 16:Screw hiding plates, 17:Door opening pad, 19:Reference stick (length to adjust structure triangle), 50:Panel0, 51:Panel1, 52:Panel2,53:Panel3, 54:Panel4, 55:Panel5,56:Panel6, 57:Panel7, 58:Panel8, 67:Panel 17]
xpart=0;
motor_offset_a = 0;

thkglass=4; // glass thickness for glass retainers

/*[Hidden]*/
diamNut3 = 6.1; // checked
diamNut4 = 8.1; // checked
holeplay = 0.16; // added diameter to ALL cylinder (internal/external)
ballplay = 0.14; // added play to ball diameter - shall give tight socket
dia_ball = 5.96; // real ball diameter

/*[Dataset]*/
htop = 0;  // height of top structure
housing_base=0; // no housing

//geometry
frame_rot = 0;
move_rot  = -30;
//Text
txtzpos = 360; // position of the message panel top
txtangle=-90;

// Data for radius 131 and height between plate 500, called HXMF 131/500
Effector_STL= "STL/Lily_30_effector_F.stl";
Hotsup_STL = "STL/Lily_31_hotend_support_F.stl";
Retainer_STL = "STL/Lily_33_effector_retainer.stl";
Cable_retainer_STL = 
  "STL/Lily_32_cable_retainer.stl";
function reference_l() = beam_int_radius*1.73205-50.9; //measure distance with a reference rod 
//radius 131 correspond to reference measure of 176mm
echo ("reference_l",reference_l());

//echo (htotal=htotal);

hbase=0; // used in simulator. the floor is at level 0
extrusion = 0;  // stop the simulator rod module
rod_dia   = 8;  // Rod diameter
lbearing_dia = 15;
rod_space = 42; //set two rods instead of one extrusion 42 is same as Fisher 1.0

top_panelthk =18;
basethk  = 18;
panelthk = 18; // structural sides
boxpanelthk = 10; //closing panels, door, etc.
cover_panelthk =10; // cover over steppers

car_hor_offset= 16; // horizontal offset of the articulation (/ rod axis)
hcar = 16; // height of the carriage
car_vert_dist = 4.5; // distance between articulation axis and carriage top
//Motor support height (46 for the Lily F)
mot_support_height = 46;
top_stop_thickness = 5;
top_clearance =  top_stop_thickness + mot_support_height; // motor 43 // clearance between top of the carriage and top structure - 5 is height of top pads, 46 is height of motor support

eff_hor_offset= 28; // offset of the effector (arm articulation axis/center)
eff_vert_dist = 0;  //vertical  distance betwwen effector plane reference and articulation axis
arm_space= 58;  // space between the arms 58
wire_space= 46; // space between the wires 46

ball_ext =1.25; // the ball cups extend over median plane by this value
dia_arm = 3;
railthk =0; 
railwidth =0; 
rail_base=0;
frame_corner_radius=0; 
frame_face_radius= 0;
corner_offset=14;
hotend_offset = 6;
hotend_dist = 17; // for STL htend file import position

beltwd=6; // belt width
belt_dist = 2; // belt FACE distance with rod axis
belt_axis = beltwd/2-belt_dist; // belt axis distance to rod axis
//echo (belt_axis =belt_axis);
motor_offset = -8; // face of the motor distance with the rod axis
motor_voffset = -23; //motor axis position/bottom of top plate

spool_diam = 200;  
spool_thk  = 70;
$spool_rot = [0,90,0];

boardwd = 100; //electronic board dimensions
boardlg = 125;

struct_color = "Turquoise";
moving_color = "Lawngreen";
bed_color = "silver";
panel_color = [0.5,0.5,0.5,0.5]; // transparent panels
//panel_color = "white";

//Indicate that the program just started (to impose camera position)
camPos = $vpr==[55,0,25];

$vpd=camPos?1750:$vpd;   // camera distance: work only if set outside a module
$vpr=camPos?[80,0,42]:$vpr;   // camera rotation
$vpt=camPos?[190,-67,290]:$vpt; //camera translation 

//sub data set of  this printer
//delta_angle = 62; 
basewoffset = 0;  // base/top panel side offset

sw_offset = -10; // offset of the switch = -10; // offset of the switch

// side plate dimensions 
splatewd = 150; // before alternative datasets
windoorwd = 150;
windoorht = 400;  
  
htsub=0; // below structure height
httop = 0; // motors on top -> 60

botrodht = 4.25; // with M4 threaded rods
posrodaxo = 70.1; // offset along axis of positioning rods
posrod_offset = 12; // offset beween bottom and top positioning rods

//belt_dist=8.5;

/*/Initial dataset - my own machine see next dataset
Delta_name = str("Lily F 131/500 by PRZ");
bed_level = 0.1; // > 0 To show surface
htotal = 426+45-13+42; // total height between plates 
beam_int_radius = 131; // radius on rod axis plane - used as reference radius
arm_length = 190; // supersedes delta_angle  
mini_angle = 25;  // minimum angle of the arms
basewd = 370; // base/top panel width 
basedp = 320; // base/top panel depth
basedpoffset = 4; // base/top panel front offset
$wallsup = 0;
rod_base  = 46; // height of the base of the rods
$ht_tens = 72; // height of tensioner frame (height of bottom of the corner)
hotend_vert_dist = 31; // dist of hotend nozzle to reference plane (ball axis)
$bedDia=200; // force the bed diameter 
//*/

//* next paragraph are alternative geometry
//- add a leading '/'  to the first line, that will uncomment whole paragraph
// and the data will supersede above data

//* Alternative dataset with same components is HXMF 139/500 - Fisher kit based
//  -> usable diameter 186 mm H centre ~ 225mm, periphery 215mm - base slightly enlarged
// uncommenting the block will supersede former data  
Delta_name = str("Lily F 139/500 by PRZ");
htotal=520;
bed_level = 20; //Support + bed heater +bed
beam_int_radius = 139;
arm_length = 204;
mini_angle = 23; 
basewd = 380;
basedp = 340;
basedpoffset = 6;
$wallsup = 0;
//Rod base shall take into account the bed level
rod_base  = 66;
$ht_tens = 92;
hotend_vert_dist = 31;
$bedDia=200; 
// stool below printer - that modify panels
// htsub=220; $spool_tsl = [92,40,-125]; 
//*

/* Alternative dataset with same components HXMS 139/530 - Scratch build
//  -> usable diameter 186 mm H centre ~ 245 mm, periphery 215mm - base slightly enlarged
// uncommenting the block will supersede former data  
Delta_name = str("LilY S 139/530 by PRZ");
beam_int_radius = 139;
arm_length = 204;
mini_angle = 23; 
basewd = 390;
basedp = 330;
basedpoffset = 1;
htotal=530;
$wallsup = 70;
posrod_offset = 5;
rod_base= -0.01;
rod_space = 58;
$ht_tens = 50;
hotend_vert_dist = 40;
$bedDia=200; 
splatewd = 160;//

//*/

/* Alternative dataset with same components HXMS 172/630 - Scratch build
//  -> usable diameter 188 mm H centre ~ 245 mm, periphery 215mm - base slightly enlarged
// uncommenting the block will supersede former data  
Delta_name = str("Lily 'S' 172/630 by PRZ"); // shall use 10 or 12 mm rods, not designed yet
beam_int_radius = 172;
arm_length = 266;
mini_angle = 22; 
basewd = 460;
basedp = 400;
basedpoffset = 6;
htotal = 630;
rod_dia = 10;
rod_space = 66;
//rod_space = 44;
lbearing_dia = 19;
$wallsup = 90;
rod_base = 2;
$ht_tens = 70;
hotend_vert_dist = 40;
$bedDia = 260; 
car_hor_offset= 18;
splatewd = 180;
// structure below floor for spool & power supply
htsub = 220; // height of the sub-base -could be whatever you want, depending spool you use + tensioner clearance
spoolsep_dp = 220; // depth of spool space - panel 15mm shorter
$spool_tsl = [115,-85,-120];
//*/

/* Alternative dataset with same components HXMS 188/800 - Scratch build
//  -> usable diameter 286 mm H centre ~ 245 mm, periphery 215mm - base slightly enlarged
// uncommenting the block will supersede former data  
Delta_name = str("Lily V 188/800 by PRZ"); // future, with 20x40 V-Slot profiles
//Movement part design to be done...
// Effector will be the D-Box effector
beam_int_radius = 188;
arm_length = 305;
mini_angle = 22; 
arm_space= 84;  // space between the arms
wire_space= 68; // space between the wires
basewd = 520;
basedp = 450;
basedpoffset = 6;
htotal=800;
$wallsup = 100;
$ht_tens = 80;
hotend_vert_dist = 40;
$bedDia=300; 
car_hor_offset= 18;
splatewd = 180;
rod_space=0;
dia_arm=6;
dia_ball =8;
corner_offset=20;
frame_corner_radius=0; 
belt_dist=8.5;
motor_offset = -12; 
eff_hor_offset= 30;

splatewd = 230;
basedpoffset = 2; // base/top panel front offset
motor_voffset = panelthk+23;
// structure below floor for spool & power supply
htsub = 220; // height of the sub-base -
spoolsep_dp = 220; // depth of spool space - panel 15mm shorter
$spool_tsl = [115,-100,-120];

//*/
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

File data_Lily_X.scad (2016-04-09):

include <Z_library.scad>  include <X_utils.scad>
// Data Set for Hexagon Minimum Delta printer -LilY - January 2015
// To be build from scratch (Lily 'S'), or with  standard Fisher components (Lily 'F')
// Copyright Pierre ROUZEAU AKA 'PRZ'
// Program license GPL 2.0
// documentation licence cc BY-SA and GFDL 1.2
// Design licence CERN OHL V1.2

part=5;
xpart=0;

thkglass=3; // glass thickness for glass retainers
$noTop = true;
$noCover =true;
$boxed = true;

if (part) { // set part =0 (no part) for delta simulation
  $fn=32;
  if (part==1) foot(); //foot with elevated support, for Fisher std rods
  else if (part==2) foot2(); // base to use with wallsup (no surelevation)
  else if (part==3) wallsup();  // wall support, in conjunction with above part  
  else if (part==4) {
    motor_support(); 
    *tsl (0,motor_offset)rot(-90)nema17();
  }  
  else if (part==5) carriage();   
  else if (part==6) tensioner(); // tensioner for plain bearings
  else if (part==7) tensioner(true); // tensioner for flanged bearings  -- add a washer between bearings
  else if (part==8) duplx (25,2) rot (180) twheel(); // option: tensioner wheel
  else if (part==9) duply (10,7) arm_junction(); // arms junction
  else if (part==10) dmirrorx() tsl (28) rot (90-22.5) extruder_bracket(); // extruder plate attach 
  else if (part==11) { 
    boardsup();
    tsl (0,-10) mirrory() boardsup(1);}
  else if (part==12) duplpartx (5, 18,11) rot(90) glasslock(thkglass);  // parameter is glass thickness
    
  else if (part==14) PS_retainer(); // Fisher power supply retainer (PS independant computer block type, Section 62x40)
  else if (part==15) Lily_plate(); // The final touch: name plate "Lily"
  else if (part==16) duplx(55) hiding_plate(); // Aesthetic: hiding screws
  else if (part==17) duply(20) door_pad();   
    
  else if (part==19) ref_stick();  // print the reference stick
  else if (part>50 && part<60)  projection() 
    rot (0,90) panel(part-50); // for panels - holes  
  else if (part>=60 && part<70) projection() 
    panel(part-50); // for panels - holes      
  else if (part==201) template(); //holes in base plate to be exported to DXF
}

Delta_name = str("Lily F 131/500 by PRZ");
holeplay = 0.16; // added diameter to ALL cylinder (internal/external)
ballplay = 0.14; // added play to ball diameter - shall give tight socket
dia_ball = 5.96; // real ball diameter

housing_base=0; // no housing
diamNut3 = 6.1; // checked
diamNut4 = 8.1; // checked
frame_rot = 0;
move_rot  = -30;
txtangle=-90;

// Data for radius 131 and height between plate 500, called HXMF 131/500
Effector_STL= "STL/Lily_30_effector_F.stl";
Hotsup_STL = "STL/Lily_31_hotend_support_F.stl";

beam_int_radius = 131; // radius on rod axis plane - used as reference radius
reference_l = beam_int_radius*1.73205-50.9; //measure distance with a reference rod 
//radius 131 correspond to reference measure of 176mm
echo (reference_l =reference_l);

htotal = 426+45-13+42; // total height between plates 
//echo (htotal=htotal);

hbase=0; // used in simulator. the floor is at level 0
bed_level = 0.1; // > 0 To show surface
extrusion = 0;  // stop the simulator rod module
rod_dia   = 8;  // Rod diameter
lbearing_dia = 15;
rod_space = 42; //set two rods instead of one extrusion 42 is same as Fisher 1.0

rod_base  = 46; // height of the base of the rods

top_panelthk =18;
basethk  = 18;
panelthk = 18; // structural sides
boxpanelthk = 10; //closing panels, door, etc.
cover_panelthk = 10; // cover over steppers

car_hor_offset= 16; // horizontal offset of the articulation (/ rod axis)
hcar = 16; // height of the carriage
car_vert_dist = 4.5; // distance between articulation axis and carriage top
top_clearance =  8 + 46; // motor 43 // clearance between top of the carriage and top structure - 8 is height of rubber pads, 46 is height of motor support

eff_hor_offset= 28; // offset of the effector (arm articulation axis/center)
eff_vert_dist = 0;  //vertical  distance betwwen effector plane reference and articulation axis
arm_space= 58;  // space between the arms 58
wire_space= 46; // space between the wires 46

ball_ext =1.25; // the ball cups extend over median plane by this value
dia_arm = 3;
railthk =0; 
railwidth =0; 
rail_base=0;
frame_corner_radius=0; 
frame_face_radius= 0;
corner_offset=14;
hotend_offset = 6;
hotend_dist = 17; // for STL htend file import position

belt_dist = 2; // belt FACE distance with rod axis
belt_axis = 3-belt_dist; // belt axis distance to rod axis
//echo (belt_axis =belt_axis);
motor_offset = -8; // face of the motor distance with the rod axis
motor_voffset = -23; //motor axis position/bottom of top plate

spool_diam = 200;  
$spool_rot = [0,90,0];
$spool_tsl = [80,60,htotal+18+15+100];

$bedDia=200; // force the bed diameter 

boardwd = 100; //electronic board dimensions
boardlg = 125;

struct_color = "Turquoise";
moving_color = "Lawngreen";
bed_color = "silver";
panel_color = [0.5,0.5,0.5,0.5]; // transparent panels
//panel_color = "white";

camPos=false; // set it false deactivate camera position (to make a film in any position)

$vpd=camPos?1750:$vpd;   // camera distance: work only if set outside a module
$vpr=camPos?[80,0,42]:$vpr;   // camera rotation
$vpt=camPos?[190,-67,290]:$vpt; //camera translation */
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

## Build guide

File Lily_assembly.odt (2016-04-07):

Lily delta printer

Assembly and commissioning instructions.

(c) Pierre ROUZEAU cc BY-SA; GFDL 1.2 – Design licence CERN OHL V1.2 – Jan-Feb 2016

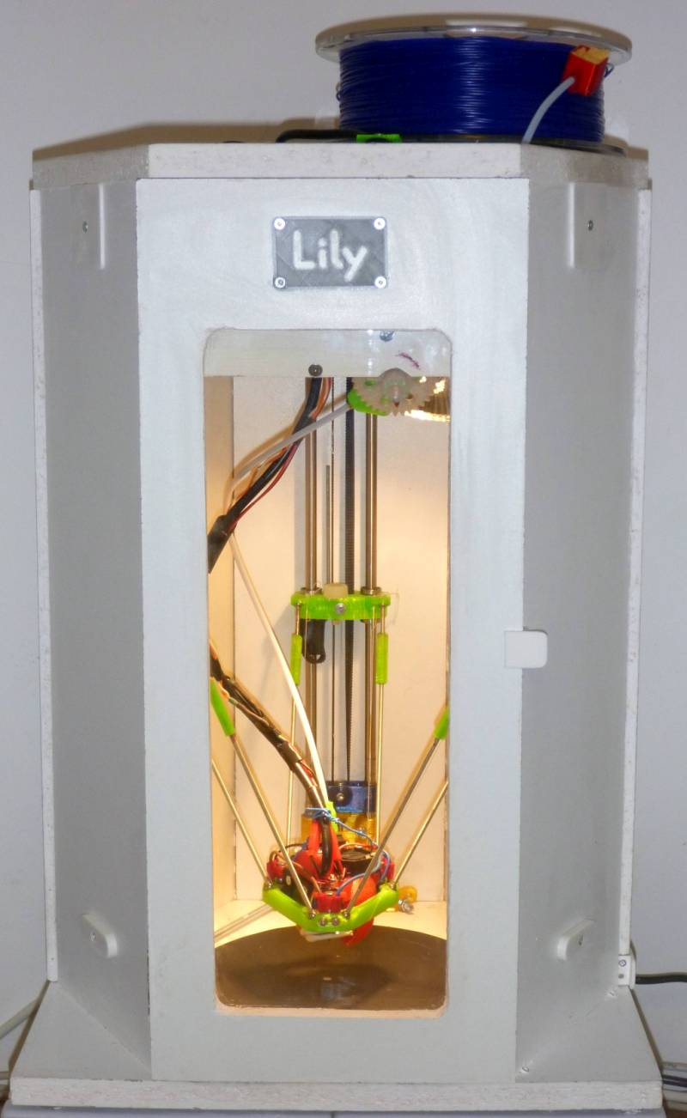
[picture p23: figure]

  References

https://github.com/Prouzeau/HXM-delta-printer

https://github.com/PRouzeau/3D-printer-spool-on-top

https://github.com/PRouzeau/Geared-Extruder

http://rouzeau.net/Print3D/ (http://rouzeau.net/Print3D/HXM)Lily (http://rouzeau.net/Print3D/HXM)

http://rouzeau.net/twg/index.php?twg_album=3DPrint%2FLily (http://rouzeau.net/twg/index.php?twg_album=3DPrint%2FHXM) Photos Gallery

Duet control board information

http://reprap.org/wiki/Duet

https://github.com/dc42/RepRapFirmware/tree/dev/Release Firmware DC42

https://github.com/chrishamm/DuetWebControl Web interface

Fisher documents.

http://forums.reprap.org/list.php?409 forum about Fisher

https://github.com/reprappro/RepRapFirmware/tree/master/SD-image

# Preparatory work

## Preparatory work

Read and look carefully the instructions, BOM, drawings, templates, photos. It shall also be interesting to look at the Fisher documents.

Choose your options (fan voltage, flanged/non flanged tensioner bearings, printer dimensions: HXMF 131/500, HXMF 139/500: from Fisher kit or HXMS 140/530:standard printer built from scratch).

There is an additive BOM list to Fisher kit.

BOM is in preparation for a 'from scratch' build with a simplified design for feet in two parts, with rods down the bottom plate, which will be stiffer. The hotend recommended will be the 'Hexagon', for its compactness and low cost.

The only critical element is the Fisher hotend, and its parts are not yet available as separate parts. Others specific parts are the extruder hobbed insert and the brass bowden end, but there are suppliers for them, see next chapter.

The duet board is available at Think3DPrint3D (Genuine V. 0.8.5) or Replikeo (Clone, yet 0.6 A – only).

## Supplying stuff

Order stuff on internet early, that may takes time to arrive (up to 5 weeks if it came from China). That shall be your first task, but you may start printing in the same time.

Screws are better supplied to an internet specialist. Except for hotend attach screw which shall be in stainless steel (on the Fisher version), other bolts and nuts could be carbon steel, but buy quality (class 8.8), it does not cost more.

It is advisable to buy spare and think to other projects.

Wood screw shall be of the best quality to not split panels. I recommend the 'Rocket'.

Suppliers :

Think3DPrint3D https://www.think3dprint3d.com The Duet board designer | Duet board, cables, hobbed insert, misc. parts
Emaker shop http://www.emakershop.com/ Managed by Fisher designer - | Miscellaneous stock of Fisher parts
Robofun.ch https://www.robofun.ch/en/ | hobbed insert, brass end, Duet board, heater block, nut
Replikeo www.replikeo.com | Duet board clone
RepRapPro China www.reprappro.com.cn | May supply to the world after RepRapPro closure

## Printing

For printing, follow the recommendations indicated in the OpenScad files. Do respect them, and notably the infill. Depending your printer hotend ability, you may prefer use 0.25mm layers instead of 0.3mm as commonly required. Note that this are engineered parts and there is no benefit with smaller layers. Dimensional accuracy is not better. On the contrary, parts with larger layers tend to be stronger.

You could print while you are preparing the wood panels and your supply. You may print first the tensioners and their thumbwheels as they are the first parts to be assembled. - The tensioners prints are not the same for flanged or not flanged bearings (not flanged bearing tensioner is untested).

It is wise to print one carriage first to check the ball socket clearance. The ball insertion shall be quite firm, it will makes its place with time.

Note that the carriage and sockets are printed for 5.95mm balls. If your balls diameter is different, you shall regenerate the STL files with OpenScad before printing.

It is preferable to print feet, motor supports, carriages and effector base on the same printer with same parameters and filament, in the same X/Y angle to have the same defaults and maintain good sliding.

For the effector base, it is important that the X/Y dimensions are equal as the ball sockets are printed.

Use X/Y scaling parameters if needed. With RepRap firmare, use M579 for X/Y scaling

DC42 and Chrishamm fork implement this (from 1.09m version for DC42 fork).

To print the duct of the HXM Standard, use the special Slic3R profile supplied.

# Manufacturing

## Drilling top/bottom wood panels

Prepare panel and drill them according templates (DXF or PDF files). Side panel shall be marked to recognize internal and external faces (as they will have recesses for screw heads).

## Cleaning printed parts

- While your parts are printed, clean them and check holes. Of importance are:

*holes for guiding rods in the foot and top support and in the tensioners. It may not be needed to clean the M3 screw holes except for the following :

* filament hole in extruder lever (2mm) ; tongue passage and bowden start hole shall be cleaned. Lever entering filament hole shall be threaded with a M4 screw.

* Motor support holes, Extruder base motor holes

* Tensioning wire holes in effector and carriages

## Belt tensioners assembly

- Install screw in tensioners (screw M4x80, countersunk head+ 1 washer medium). Use two nuts for tensioning manoeuver, you may add the mini thumbwheel (the inserted nut is on tensioner side) or left just nut/counternut. There shall be minimum play between thumbwheel and tensioner. Nuts shall be locked with screw and well tightened. Note: this is very difficult to dissassemble, so be cautious.

Install the bearings according photos, using toothpick as a temporary maintainer for the two bearings. If you are using flanged bearings, it is imperative to add a washer (thickness ~0.8mm) between the bearings to limit belt friction on bearing flanges.

Plain bearings shall be pushed sideways as the belts guide hinder top entering. Installing the screw will push away the toothpick.

## Carriage assembly

Assemble bearings on the carriage. Beware, this is not symmetric. Long bearing is on the left while looking the carriage with arms articulation facing you. Screw rubber stops. You may not need a nut and could screw directly in the plastic. M3x20+medium washer.

Somewhat grease the internal of the bearing. Use lithium bearing grease. White grease in spray is useful.

## Pre-assembly of one column

- Pre-assemble one column and use it to drill the side panels holes. There are positioning holes diam 3mm in motor and bottom support. Beware of good perpendicularity between the rods and supports.

- End to end supports shall be exactly the same length as your panels (in principle 500mm).

- Install the carriage in this pre-assembly to check the sliding is good and your printed dimensions are accurate.

## Drilling wood side panels

- use the preassembled column

- Motor holes in panel shall have a recess on the outside face for screw head of 4mm. It shall not be too deep, as the thread is blind in the motor.

- there shall be a hole diam 10, depth 5mm facing the motor shaft

- The clearance between tensioner and panel is minimal. So you could either grind the end of the bearing screw in the tensioner or make a 2mm recess in the wood panels facing the tensioner bearing. (the movement of the tensioner may not exceed 5mm)

- Disassemble the column

# Assembly

## Frame assembly

- Install the tensioners nuts in the column feet. A vise may help.

- Assemble top and bottom triangles. There is a calibrated stick you could print, or if your printer is too small, cut in any material. For the shown dimensions (internal radius 131mm), this stick is 172 mm. Look photos to see how to position them

- Make the positioning hole in your top plates sufficiently large (diam 6mm) as they shall not force on the triangle, to have it remain with accurate dimensions

- Check carefully that the belt tensioners are easily sliding on the rods. You may use paraffin to help

- Before installing the bottom triangle, check your tensioning nuts are still there.

- Clamp the bottom triangle on the plate

- Punch precisely the bottom fixation holes

- Use wood screw for bottom triangle assembly. Alternatively, you may do larger holes (diam 6) and use M4 bolts with washers, which may limit the side forces on the column foot for good accuracy

- If not already done, check the foot rod hole are cleaned and of appropriate diameter. Insert the rods in foot while hammer gently with a mallet to not destroy feet.

- Introduce carriage in appropriate position

- It is better to install the belts now, as installing them later (from the top plate hole) may be a bit more difficult. You need to make a 1mm hole at the end of the belt to pull it with a rigid wire around tensioner bearing. Note that as on the fisher, this is the back of the belt which run on bearings and the belt is twisted on return path.

- slide motor support on limited length and check that the sliding is ok then slide it to final position.

- Bolt the side panel on the feet with rod tightening screws (M4x50, domed headin diam 6 holes). Tight moderately.

- Set the frame upside/down. Beware, not completely assembled, it is a bit fragile.

- Install clamps to prevent panel splitting while tightening wood screws. Set wood screw (4x40) and tighten firmly. Remove clamps.

- Return your frame in normal position and tighten the side panel attach M4 screw

- Punch holes in the feet support and install wood screws.

- Check your motor supports are flush with side panels (use top plate)

- Prepare motor screws M3x40, flat head. They may be a bit difficult to install, so slightly grinding their end conically may help. Pre-install them in panel with Medium washer. Don't use hex head screw as I have done, because you can't push them in place (I set spring in my socket spanner to push the screws). I ended to install M3 rods then cutting them to replace some screws.

- Make a loop with the end of your belt and position your motor inside the belt loop

- Screw the motor in place

- Install top panel and attch with wood screw 4x40. Use clamps as before

- Install three rubber pads as feet and two pads on the back of the base plate.

## Arms assembly

Balls shall be glued to rods.

Make a mark on rods before screwing them, to avoir overscrew, which destroy the link part.

All rods shall have the same length. If you cannot measure the arm length, make a template to check all arm length are identical. You will be able to evaluate the arm length by printing calibration parts.

The arm length is axis to axis, so the measured length does include ball diameter, e.g. for 190mm, with 6mm balls, you shall measure 196mm. Measure your ball diameters.

## Effector support assembly

Screw the standoff with domed head screws M3*12.

Wire the three pair of standoff to make a continuous circuit done by the balls, as on the Fisher Bed with two links and the cable connected on the remaining pair. The eyed terminals shall be installed inside, with bulge turned on the outside (look photos). These terminals shall have a sufficient clearance to have their bulge just above the effector. This is not the case of the original eyed terminals which unfortunately cannot be reused.

Instead of what is done on prototype, you may wire only one pair of standoff. For this to work properly, you shall have a weaker rubber on the side of the wired standoff pair, which is delicate and then not recommended.

## Hotend assembly

The hotend itself shall be assembled per RRP instructions, and if you get it from a Fisher, this is already done and left unmodified.

Hotend attach to support. Support shall be in ABS or PETG or other heat resistant plastic, as temperatures may go up to 60°C on hotend fins. The fin block is not in contact with the support (there is an insulating gasket) but the screw do conduct heat and is ~10°C below fin temperature.

4 bolts Bolt M3x35, countersunk head, STAINLESS STEEL A2 or A4 , 8 washers M3 medium.

The hotend support part shall be well cleaned, preferably with a sharp cutter to have good airflow. This is a bit critical. There are some flats parts set for bridging which shall be cut to enter the hotend in its place. The hotend fan bottom part shall but cut internally reclined to the hotend (the gasket will maintain tigthness), which is also needed because the bridging make this not very nice.

The bridging area at at outlet of the hotend duct probably need to be filed. A slight chamfer (0.5 mm) may be cut at the outlet. (part thickness ~1.2 mm).

1 plumbing fiber gasket 20/27 (3/4”) thickness 1.5mm. Shall be cut internally to a diameter of 17mm (hotend fin diameter). Passage for screws are drilled in place while cleaning the holes in the hotend support.

Bolts on fan side are installed with head on gasket (with a washer), bolts near center will have the nuts on gasket (also with a washer). You will have to rotate the hotend to allow passage of screwdriver. Do it gently and tighten later with the nuts.

You will have to install the balls of the kinematic support. Glue them on their screws.

Fan holes shall be drilled to 3mm. Attach to the support with wood screws 3x15.

## Extruder assembly

See the instruction for the geared extruder in dedicated documents.

The extruder is installed on a plate attached to side panels. It is inclined by 22.5° from vertical.

There is a template for HXM131 (with the board top panel drilling template), the width will be larger for the HXM 139 – to be defined how much.

There are printed brackets which will give you the proper inclination. Use the bracket assembled on the plate as a template for marking holes to be done on the side panels.

For HXM 131, the top of the extruder plate support shall be at 68mm from the bottom of top plate.

## Bowden tube assembly.

For HXM 131, Bowden tube length shall be at least 420mm (this is the original length on the Fisher)

It may be sufficient for the HXM139, but you may have to lower somewhat the extruder plate (by ~ ~10mm, this shall be checked).

Follow closely RRP instructions. You may experience filament blockage if Bowden tube is tightened too firmly in the hotend, so I always unscrew by ½ turn after assembly on the hotend.

## Tensioning wire installation

Use Nylon wire 10kg. Use [['8' type knots→http://www.animatedknots.com/fig8_/#ScrollPoint]] on looped wire as they are bigger knots and less prone to break.

- Install effector in place (without hotend), the socket ball grip shall be sufficient to maintain it without the wires.

Cut 3 time 1m length of nylon wire.

- Makes a loop with a return branch of 100mm, Tape the return branch.

- Make at least three 8 knots with the loop on the end to block passage in holes. Pass the wire in wire hole in carriage from top to bottom, then in same side effector hole, then make a turn around the side of the effector (to avoid conflicting with the hotend support), then pass in the other arm side of the effector (top to bottom), then in the other side of the carriage. Mark color with a marker 30mm after the outlet of the wire.

- Remove arms to be able to pull the wire and make knots.

- Make a loop folded at the mark, Tape the loop. Make at least three '8' knots, with the loop end at ~ 15mm from the knots.

- Reinstall arms and check tension. Shall be between 500g and 1 kg, but that is a bit difficult to evaluate.

- Remove arms and add knots to increase tension if needed.

- Repeat for other sides

## Wiring the fans

Fan is supplied in 5V and the current is sunk by a MOSFET on the negative side of the fan. However, on the Duet, there is a LED to indicate fan operation, which means that sunk pin could be supplied in 19V through the LED when fan is not in operation. So a protecting diode is installed, but in 5V, the forward voltage reduce significantly the fan power and a low forward voltage diode shall be used. I choose SB340.

If you are practicing electronics and are handy, you may remove the fan LED instead of adding a protecting diode.

VERY IMPORTANT: On the Duet 0.6, The sunk pin is the pin inside, the outside pin is supplied in 19V and a mistake will send 19V on the 5V supply and will burn the board. Check the photo, my board is still alive (...). The Molex connector will orient the plug.

Beware of boards which are supplied with simple pins instead of Molex connectors (this is the case of my Duet 0.8.5 on The D-Box), that is very dangerous and a mistake take only one second to smoke your board.

## Other wiring

Look at the Fisher installation procedure. If using Fisher kit, one motor cable shall be lengthened. Be cautious, a contact fault in the wiring may burn a driver, hence your whole board.

Beware of the original RRP power supply plug, if the cable pull sideways, you could have a short in the plug. Bending plug tabs may help. Hopefully, in case of a short there is a protection in the power supply block which make clicking noises. This is why the plug have been replaced by a cable.

The effector cables shall be poreferably groupes in a textile sleeve. This is better for maintenance than zip-ties.

The effector cables shall be braced to the effector to maintain it vertically and avoid conflicts with the carriage. See photo.

All motor cables shall be attached to the top structure and shall not move. Best is to use zip-ties.

The effector cable shall be alone in the top hole through to not move other cables. A retainer shall be installed to avoid any cable movement atop the board.

## Hotend support installation

Look photos.

I use slices of old bike tire tubes as rubber 'springs'.

Depending your tube size, there may be two rubber turns on the hotend support arm, but the attach to effector shall be with one turn only. Use rigid wires to pull the rubber on effector attach, this makes installation easy.

# Commissioning

## Updating software and firmware

UPDATE the firmware to the last version of DC42 fork. See page on RepRap Wiki for the update.

UPDATE the web interface (all content of www directory) if you have a recent version of DC42 fork. Web interface as found in the Fisher image won't work. Edge/IE have issues with the web interface

Take the image of the HXM, or, if not available, the image of the Fisher.

Update the image with the following HXM files :

- Configuration file (sys/config.g)

- Homing file (sys/homedelta.g) for operation without end switches

- Calibration file (sys/bed.g) – shall be adapted to your machine (see calibration paragraph)

- Interface file (www/js/interface.js)

- Miscellaneous macros

## Commissioning

Mechanical commissioning. Make a general control of the printer mechanics, check all screw tightening, plays and especially cable clearance while moving the effector. It is especially important that the cable didn't go in carriage way while homing the printer. For full diameter use, you shall cut (with a saw, not with disk) the bottom rod located on the fan duct side, as the part fan duct will conflict with the rod at maximum printing diameter.

Use RRP commissioning procedure for Fisher except:

- enter http://HXM in your browser to access to the machine web interface.

- Without switches, the available height defined in M665 is not used, you shall define the height in the 'homedelta.g' macro. Start with a height smaller than expected, so when the effector goes to 0, it is above the real 0.

Note: during automatic calibration, if the sensor is triggered before the hotend is lowered down, this is because the bowden tube traction is lifting the hotend support of the effector, triggering the contact. IN that case, you shall reinforce your rubbers, see the paragraph below 'Checking sensor triggering force'.

After doing the RRP commissioning, you shall do :

- Calibrate your extruder. Bowden tube disconnected, make a mark on your filament, cold extrude 1000mm of filament, make another mark, measure, and correct the value steps/mm (its G-code M92 in config.g file).

New step/mm = Old Step/mm * 1000/measured length (in mm).

Code 'T0' , then 'M302 P1' (allow cold extrusion), then 'G1 E1000 F2000' (extrude 1000mm)

To retract 'G1 E-1000 F2000' then 'M302 P0' to prevent cold extrusion.

Nota: code 'M84' shut down all motors

- Thermistor ADC checking (look RepRap Wiki duet page links)

Sensor offset adjustment (H parameter in bed and bed_report macro)

There is more offset on the side than in center (this is reverse of the Fisher, where the offset is larger at the center).

Bed, bed_report and P0 to P6 macros shall have same coordinates and be adjusted while you displace probing points, which may notably be needed if your bed surface is weraed (as could occurred easily with BuildTak) or for a different usable diameter.

To test the offset, you shall :

Do at least 3 calibrations till you get consistent results.

Execute M665 and note the reported parameters to modify your configuration file.

Please note that if you use the homing macro without end switches, the height in M665 will not be used and the height shall be modified in the homedelta.g

Move to the calibration points with the P0 to P6 macros and lower the head manually atop a paper sheet till the paper sheet began to have difficulties to slide.

Repeat for all the probe points, note the values on a paper.

You shall then modify the H parameters in the bed.g file and reload this file on the SD card. I find the FTP the easiest method for that.

Values found shall be substracted to the already defined offset, meaning that if you find +0,1 and the offset is already -0,22, you shall do -0,22-(+0,1) = -0,32

If using a ‘BuildTak’ surface, you shall not ‘crush’ the filament on the surface and the resulting value while paper began not to slide shall be within – 0.1~0,12 mm , so you shall substract 0,12 to lift up the hotend, say if offset is -0,25 while paper is sliding at exactly 0, you shall set -0,36.

After adjustment of H parameters in bed.g, modify the bed_report.g with same values, then reload bed_report.g on the SD card and run the macro.

If your paper report is neat, but the results of the calibration and bed_reports shows differences, that means that your bed is not flat. What count is the paper measure, not the calibration result, so do not cheat by modifying the H parameter to obtain a very low calibration value.

Note that all macros could be run after being loaded on the SD card by FTP, without rebooting or restarting.

## Checking sensor triggering force

Shall be from 800g to 1200g. Note that the Z offset of calibration points depends from this force, so if you change the rubbers, you may do a new test of calibration.

Use a kitchen scale (on support to clear the triangle rods), and lower the effector with the manual commands till triggering the sensor (web interface shall be parametered for 0.05 mm displacements). You shall home your printer before installing the scale if you want to avoid heavy impact on the scale !

Adjust your rubbers if load is excessive or insufficient (you may play with their width). The rubber shall be well inserted behind their retaining bars.

## Miscellaneous

There are very few modifications between the prototype and the documents supplied. One of those is that the back panel is now full width. This is for:

* Installing a fume recycler on activated carbon pad (like on the D-Box) on the left. See new photos

* Having place to install tools on the right of the back panel, which will be more elegant than on one of the front panel (and more roomy also). A door have been added. See photos

End switch holder is not finalized, as there is no switch on prototype, for simplicity and reliability. However, the design was started and could be found in the OpenScad file.

Acronyms :

RRP : RepRapPro company, Fisher designer and supplier, closed its doors mid January 2016.

TBD: To be done

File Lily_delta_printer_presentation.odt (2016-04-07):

LILY F delta printer

Presentation

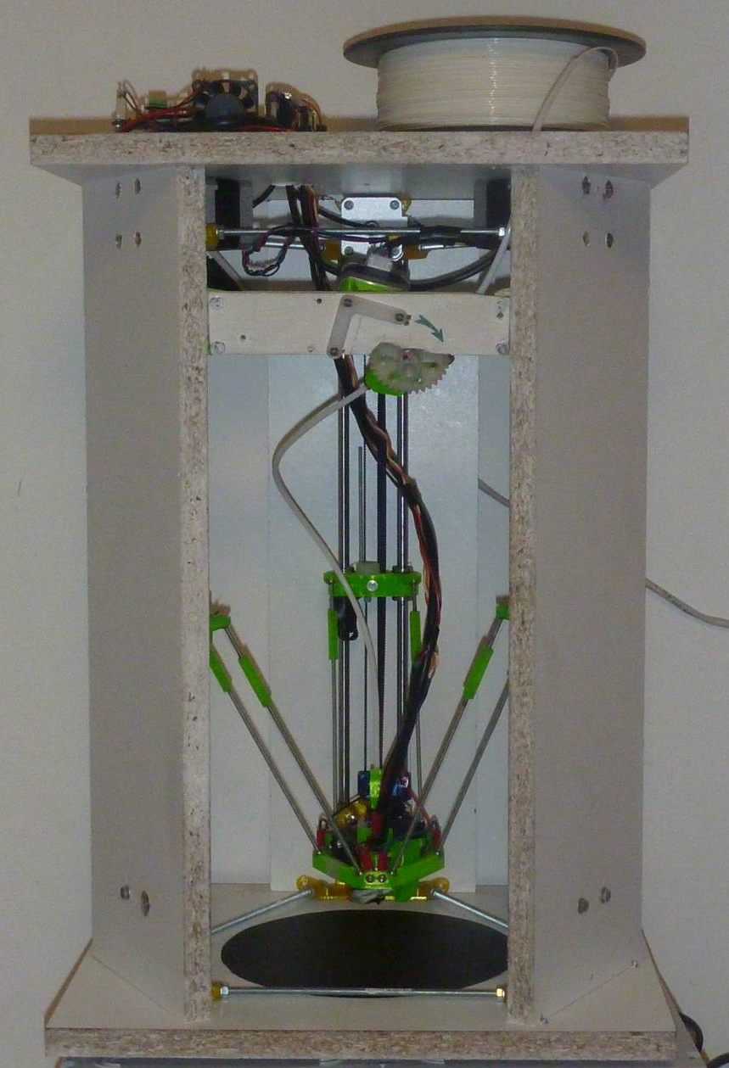
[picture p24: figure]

Based on my experiences on the Fisher and the creation of the D-Box printer , I developed a new printer, the Lily F (formely named HXM) which was meant to use the Fisher delta components. It was designed to be used with the Fisher mechanical kit, but with RRP closure, it does have lost some interest as it is now.

The ‘F’ version is using Fisher kit parts, while the ‘S’ version is built from scratch.

Its really usable space is diameter 185mm, 240mm height at center and 220 mm height at 185mm diameter. Base size is 320x370mm, with 500mm between plates. That is roughly twice the really usable volume of the fisher (which is 140mm diameter, ~90mm height at 140mm diameter and 180mm at center.

Note that prototype was built with 170mm diameter, slightly higher usable space and was slightly smaller.

References :

https://github.com/Prouzeau/HXM-delta-printer

https://github.com/PRouzeau/3D-printer-spool-on-top

https://github.com/PRouzeau/Geared-Extruder

http://rouzeau.net/Print3D/HXM

http://rouzeau.net/twg/index.php?twg_album=3DPrint%2FHXM Photos Gallery

My aim was to:

- Having a more silent printer

- Having a part fan controlled by the board

- Got rid of all acrylic and fragile parts

- Few mechanical adjustement

- Being capable to enclose the printer.

- Increase the printable dimensions

I have done like on the D-Box, with the kinematic positioning system moved from the bed to the effector. Globally the effector weight is increased by 10g (including balls), which is compensated by the lighter arms.

For the arms, I have not changed the winning team and they are made with M3 threaded rods. This is relatively light and super strong. I was capable to lift the printer (8kg naked) by its effector. Don't even try that with a Fisher, even if its weight is less than half that.

Please note that you can use this effector and carriages on a Fisher, without diameter loss, the height loss being compensated by the bed removal. The big advantage is that the Fisher bottom plate may be much more flat than the Fisher bed. The rod space is the Fisher 1 (42mm), but that could be modified.

The arms are made as on the D-Box, with balls in printed cups, maintained with tensioning wires. I discovered experimentally that a good tension creates friction and dampen vibrations, reducing the ringing on parts. I used nylon wire instead of high grade Dyneema, and this is simpler to install and with elasticity of nylon, there is no need for springs. Tension is just made by adding knots on the wires. I will see if it is as durable as the Dyneema/Spectra.

There is no end stops for simplicity and reliability (while they could be installed). The motors are stalled while carriage is locked on its top stops. That makes quite a bad noise while stalling, but precision is not that bad if you use a not too low current.

The difficulty of delta printer is positioning, so I use threaded rods to make the triangles. On the bottom, they should be cut after assembly for effector/bed clearance (at least one to use the maximum diameter without conflict with the fan part duct).

The assembly is faster than the Fisher, but you have to do some woodwork before (quite easy) and modify and complete the wiring (fairly tedious). Closing the box add some work with the hinges installations and recycling system, but this is highly recommended.

Plastic parts are printed in PETG, and so, all components have been reinforced compared to the Fisher, because the PETG stiffness just above half of the PLA stiffness.

I have used two high quality Sunon 20x20x10 fans (5m3/h),supplied in 5V, which are extremely silent. They are not that powerful, but that seems to work. Hotend cooling is not perfect, but seems not worse than the Fisher, however, plastic parts are more exposed to heat (insulation is done with a plumbing fiber gasket).

This fan setup works, however you shall be very cautious while wiring them. Check and recheck polarity on the controlled fan, a mistake will burn the board (sending 19V on the 5V input cannot be nice) . It is safer to use 12V fans, but it needs a DC/DC converter.

- I simplified the already designed spool on top system, with no bearings neither any mechanical part. Its works better !

- I improved a bit the already designed extruder, with stiffer bearing holders. As I already experienced on the Fisher, a good position of the extruder is fairly difficult to establish. I tested 6 positions before settling on the final one. But this allow to use the original bowden tube of the Fisher ( I have to lengthen mine, which was reduced with my spool on top installation, but this extra-length is the original cutted part...).

Does it work ?

It is really the beginning, but for now, I don't see significant differences with the Fisher. I have not printed large parts, anyway.

As for the noise, there is a huge improvement. Indeed, it is a bit less noisy than the D-Box, which is enclosed. Enclosing it will improve noise, as everything is inside.

What are the drawbacks and compromises ?

- There is a bit more than twice the weight in plastic (total ~350 g), which translate in a bit less than twice the printing time (parts are globally more simple). They are printable on the Fisher, however I printed them on the D-Box, which is faster in PETG because of its hotend and controlled cooling, mostly with 0.3mm layers.

Total printing time ~16h on the D-box, maybe 20h on the Fisher.

- The fixation of the hotend on its support is improvable, indeed I redesigned somewhat this, but this is not yet tested.

- For weight and dimensions reasons, I have not used magnets to maintain the hotend like on the D-Box, instead I used rubbers cuts in bike tire tubes. This is less practical to install, but I find a reasonably easy way to do it. So, in case of mechanical trouble, that is not the hotend which is ejected, but the arms which pops out (I tested during commissioning...).

- You have to order a few stuff (2 fans, a diode, cables and connectors, some M3 screws, a larger buildtak, 25cm of bowden tube for filament inlet) and buy parts in DIY stores (wood, to be cut by the store for accuracy, M4 bolts and nuts, wood screws, M5 rods, M3 rods, rubber supports, nylon wire, aluminium sheet for board shielding), for a total which may not exceed 50 euros.

- Alas, like on the Fisher, you will not escape to do some manual calibration as the offset on the calibration points is not constant, because on the center, you are using 3 belts and near columns, mainly one belt is used, so the offset is larger on the periphery (this is in reverse of the Fisher, where offset is larger at center due to spring loads). But with recent version of DC42 fork, it is a bit easier to do, but a procedure have to be written. Macros P0 to P6 which move the effector to the calibrations points helps that.

- The effector plug installation is really messy. On the D-box, I wired directly to the board and find it much more simple, with minimal drawback as the route is direct and so wire replacement easy. The best installation may be to use a sleeve instead of zip-ties to group independent cables.

Ah, and printing on melaminated chip board did not work, even with glue. So I have installed a BuildTak surface, which is efficient, but quite fragile. See specific advice file for BuildTak use.

Credits:

- Tim Jacobsen, for the rod system with wire tensioning system.
- RepRapPro company, for the idea of kinematic positioning system used as a sensor, but here I set it on the effector instead of the bed.

© Pierre ROUZEAU cc BY-SA – GFDL 1.2 -

first issue 17 Jan 2016 - rev 7 april 2016

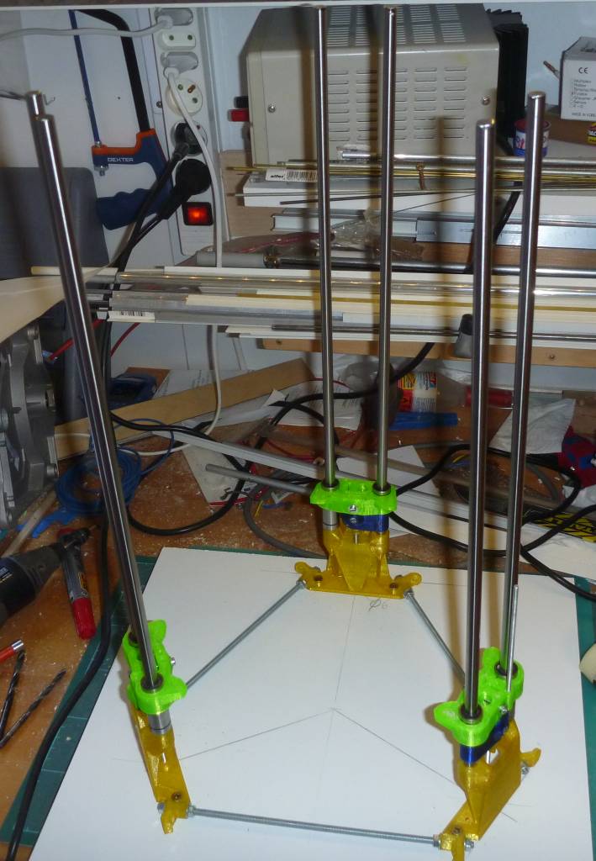
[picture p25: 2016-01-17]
Photos/Lily_F_assembly2.jpg

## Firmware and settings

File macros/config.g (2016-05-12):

; Configuration file for Lily 'F' 131/500 by PRZ - delta 3D printer
; (c) Pierre ROUZEAU  April 2016 - cc BY-SA, GFDL 1.2
Shall use recent version of DC42 Fork - 1.12 or later and DWC 1.11 or later
Note that these DC42 recent versions need at least version 1.08 of the web interface

; Communication and general
M111 S0                             ; Debug off
M550 PLily				        	; Machine name (use http://Lily for web access, can be anything else) - Netbios name
M551 Preprap                    	; Machine password (used by FTP AND web interface)
M540 P0xBE:0xEF:0xDE:0xAD:0xFE:0x43 ; MAC Address - shall be different for each machine on the same network
;*** Adjust the IP address and gateway in the following 2 lines to suit your network
M552 P0.0.0.0                  		; IP address - to be defined if the machine is not recognised by name
;M554 P192.168.1.1                  ; Gateway
M553 P255.255.255.0                 ; Netmask

M555 P2                             ; Set output to look like Marlin
G21                                 ; Work in millimetres
G90                                 ; Send absolute coordinates...
M83                                 ; ...but relative extruder moves

M106 I0 ; fans 						; for 0.8.5 board, you shall use recent DC42 versions
M106 S0 ; Turn off Fan 0 (backward compatible with older firmware)

; Axis and motor configuration
M569 P0 S0							; Drive 0 (X) goes forward - adjust depending your configuration
M569 P1 S0							; Drive 1 (Y) goes forward - adjust depending your configuration
M569 P2 S0							; Drive 2 (Z) goes forward - adjust depending your configuration
M569 P3 S0							; Drive 3: extruder - adjust depending your configuration
; beware old firmware version, extruder was P4
; instead of reversing by software, the motor plug may be inverted (imperatively POWER OFF, that may kill the board)
; if this is feasible (non polarized plugs)

;M574 X2 Y2 Z2 S1					; set endstop configuration (all endstops at high end, active high)
M574 X0 Y0 Z0 S1					; set endstop configuration (no endstops)

M665 R87 L190 B85 H243.41 X0 Y0		; set delta radius, diagonal rod length, printable radius, homed height and tower angle
; beware that without endstop the height is defined in the homedelta.g and supersedes this value
M666 X0 Y0 Z0			 		 	; put your endstop adjustments here
M92 X87.489 Y87.489 Z87.489  		; Set axis steps/mm
M906 X1000 Y1000 Z1000 E1100 I45	; Set motor currents (mA)  I45 is the idling percentage (default 30)
; beware that the values defined above for X,Y,Z are redefined in the homedelta.g and supersedes the values defined here
M201 X5000 Y5000 Z5000 E2000		; Accelerations (mm/s^2) 
; beware that the values defined above for X,Y,Z are redefined in the homedelta.g and supersedes the values defined here
M203 X15000 Y15000 Z15000 E3600		; Maximum speeds (mm/min)
M210 Z50                            ; Homing feedrate - not used ?
M566 X1200 Y1200 Z1200 E600			; Maximum instant speed changes mm/minute  !!extruder max speed change from 1200 to 600

; Thermistors
M305 P1 R4700                   	; Put your own H and/or L values here to set the first nozzle thermistor ADC correction
									; to compare values, your ADC shall be calibrated ! see commissioning

M143 S300							; maximum hot-end temperature  - default 260°C
									
; Tool definitions
M563 P0 D0 H1                       ; Define tool 0
G10 P0 S60 R60                     	; Set tool 0 operating and standby temperatures
M301 H1 P12 I0.25 D70 T0.21 S0.7 W150 B20;temperature control PID for hotend insulated with Kapton
;M572 D0 S0.05 		; elasticity compensation for the Bowden tube, 1rst extruder - abandoned due to high vibration on extruder
M92 E420.0;  !! extrusion rate, with supplied geared extruder - copied from Ormerod, nearly exact
// for direct drive extruder, the value may be from 140 to 150
// you SHALL calibrate this value, do not rely on defaults

;// Z probe and compensation definition
M558 P4 X0 Y0 Z0 H2					; Z probe is a switch and is not used for homing any axes
G31 X0 Y0 Z0 P200			    	; Set the zprobe height (offset) and threshold (put your own values here)
; Z offset is defined as 0, because the values are defined for each calibration point in bed.g

; Geometry correction
M556 S78 X0 Y0 Z0                   ; Axis compensation here (X/Y/Z not perpendicular)
M579 X1.0068 Y1.0068				; Part scale (here the calibration part was smaller than required) - adjust to your own measures

M404 N1.75 D0.4						; Filament diameter 1.75, nozzle 0.4 - used by web interface only

M98 P/macros/startmusic.g			; Macro play music with steppers, indicates board started, stepper and drivers ok

;Useful G-codes
;M206 Set home offset. Could be used to adjust head above bed during printing. M206 Z0.1 move up by 0.1mm 
;M999 reset board
;M562 reset a temperature fault
;M105 get current extruder temperature
;M141 get or set chamber temperature
;G28  home
;G32  calibration standard (use macro bed.g if present or use points defined by M557)
;M302 P1  allow cold extrusion for P1 extruder
;M503 Display this config
;M577 wait an endstop trigger - see RepRap wiki
;M997 In application software upgrade - in development
;M668 Set bed errors compensation - in development - Very interesting feature to compensate non flat or temperature deformed bed

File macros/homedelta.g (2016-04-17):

; Homing file for RepRapFirmware on D-Box - NO BED - reduce height if there is a bed
G91							; use relative positioning
;******* Change F500 in the following line by F5000 when you are finished commissioning
M906 X500 Y500 Z500         ; low current for homing against mechanical stop - shall be at 480 mini
							; 200 don't move, 300 move partly, 400 move ok, 450 jumps when homed 500 ok
G1 S2 X320 Y320 Z320 F3000	; move all carriages up 300mm S2 no stop detection
;G1 S0 Z520 F4000	; move all carriages up 520mm S0 no stop detection
;G1 S2 X-4 Y-4 Z-4 F1000	; move all towers down 4mm
;G1 S2 X8 Y8 Z8 F500		; move towers up 8mm, stopping at the mechanical endstops
M906 X1000 Y1000 Z1000      ; return to normal current
G92 X0 Y0 Z243.41			; defines the position when homed  - required while there is no endstops - beware assymetry
G1 Z-10 F500				; down a few mm so that we can centre the head
G90							; back to absolute positioning
G1 X0 Y0 F2000				; centre the head and set a reasonable feed rate
G1 Z20 F12000				; down near bed

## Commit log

2016-01-17 First issue
    HXM delta printer, based on mechanical components of RRP Fisher. Usable
    area diam 170 mm x 242 mm or diam 186mm x 225 mm. See Photos
    subdirectory
    [Delta_simulator.scad, Effector_HXM.scad, HXM BOM.ods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]
2016-01-17 Added BOM in pdf - better BOM formatting
    [HXM BOM.ods]
2016-01-17 Fix bug on foot height - belt view
    [Delta_simulator.scad, data_HXM.scad]
2016-01-18 Improvement of hotend and part ducting, forgotten STL files
    With relatively small fans, good ducting is critical and both hotend and
    part duct have been improved with good results. Better part duct
    improved bridging and overhang . Less play in hotend duct reduced the
    lower fin temperature by 5~6°C (58->52°C with hotend at 285°C) .
    [Effector_HXM.scad, HXM_Effector.stl, HXM_cable_clips.stl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]
2016-04-07 Revised documentation and photos, add accessories, add film
    [Delta_simulator.scad, Effector_HXM.scad, Effector_Lily_F.scad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]
2016-04-07 minor mod to remove warning
    [data_Lily_F.scad]
2016-04-07 Update with box
    [Delta_simulator.scad, Lily_30_effector_F.stl, Lily_31_hotend_support_F.stl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]
2016-04-07 add spigots
    [Spigot90.stl, Spigot95.stl]
2016-04-08 Panel projection - default size now 139/500
    [Delta_simulator.scad, Effector_Lily_F.scad, Lily_F_139_500_51_front_panels.dxf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]
2016-04-09 Panels update - rename OpenScad library
    [Effector_Lily_F.scad, Lily_F_139_500_55_left_door.dxf, Lily_F_139_500_56_right_door.dxf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]
2016-04-09 readd library utility with old name
    file is identical to Z_library.scad, re-filed for users with old data
    set
    [PRZutility.scad]
2016-04-10 Rotating video and dual format (no sound on Firefox with mp4)
    [data_Lily_F.scad]
2016-04-17 Add/updates macros
    [Allow_cold_extrusion.g, Extrude_1000mm.g, P0.g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]
2016-05-12 Update config M301 & M143
    [config.g]
2021-04-22 Misc. updates - change default size
    [Delta_simulator.scad, Effector_Lily_F.scad, Lily_32_cable_retainer.stl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]

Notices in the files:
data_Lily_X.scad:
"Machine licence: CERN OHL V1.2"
